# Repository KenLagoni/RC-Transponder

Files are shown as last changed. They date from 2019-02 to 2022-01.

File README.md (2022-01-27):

# RC Transponder (Locator Beacon)
After spending hours/days/weeks searching for lost RC Planes, I decided to design a single piece of hardware which can survive a crash and keep transmitting the GPS location.

## Design
<h4>The latest hardware version 12:</h4>

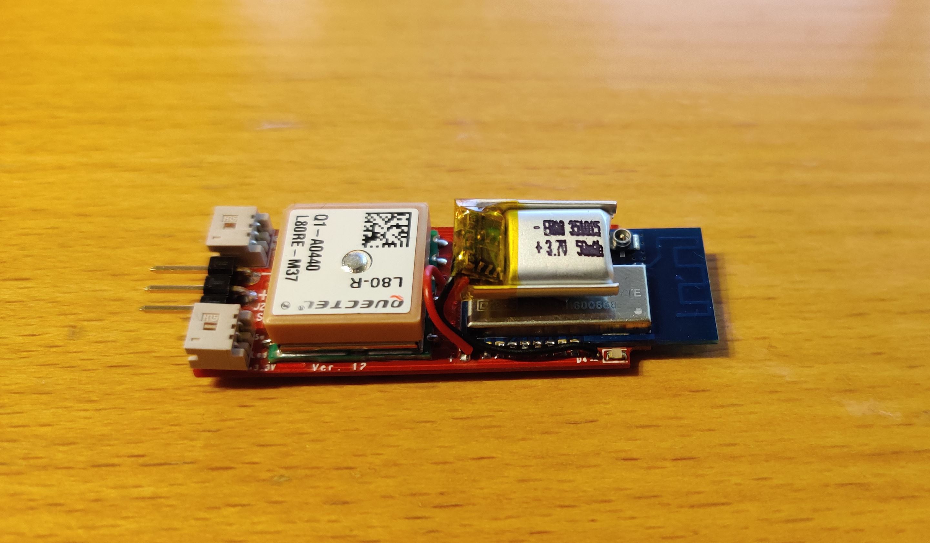
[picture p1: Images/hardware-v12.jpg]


### Features (Crashed mode)
1. Get GPS coordinates from on-board GPS sensor.
2. Keeps operating if power from plane is lost (like in a crash). 
3. Continue to operate after a crash for ~14h with a beacon transmitted every 10 second.
4. Recharge onboard battery from planes power supply. (50mAh Lipo cell)

### Features (Normal mode)
1. Operate as primary Frsky GPS sensor ID4 on SMART Port (using [pawelsky's](https://www.rcgroups.com/forums/showthread.php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) library).
2. Opperate as Mavlink to Passthrough converter for [Yaapu](https://github.com/yaapu/FrskyTelemetryScript) telemetry script for OpenTX.
3. Outputs other transponders location as StatusText messages via Passthrough to the Yaapu script. This means that when flying it can be used to listen for a crashed plane. This way other transponders will be displayed on the Radio:<br>*"ADSB([CALLSIGN]): [GPS_LATITUDE],[GPS_LONGITUDE],[NUMBEROFSAT],[FIX(2d/3d)],[HDOP]"*

### Features (Locator mode)
1. When placed in module bay of a radio running OpenTX, it will listen for other transponder beacons and send there coordinats to the Radio as seconday GPS sensor (ID5).

### Settings*
1. When connected via USB to a PC, it will show as Serial(COM) port and simple commands can be sent.
2. A unique callsign (up to 8 charactors) can be set via USB port (setcallsign [callsign]). 
<br>*(Settings are stored in NVM and only cleared when flashing new firmware).

### CPU (ATSAMD21 - ARM Cortex-M0+):
This project uses the SAMD21 MCU from the the Arduino MKRZero.

### Radio module (EBYTE E28-2G4M20S 100mW Lora):
In order to reduce size of the antenna, I tired the 2.4GHz modules from EBYTE.
I tested the EBYTE E28-2G4M20S (100mW) found that when using Lora modulation with SF7, BW= 400KHz and CR=4/5, I could get a range of ~2km between two modules.

### GPS Sensor (Sierra Wireless PA6H or Quectel-L80-R):
The PA6H from Global Tech (now Sierra Wireless) was the smallest GPS I could find with a decent chip antenna. (UBLOX CAM-M8 was not tested but could also be relevant).
The PA6H only transmit NMEA strings, so the CPU has some extra Work here.
On Hardware version 12 the GPS was changed to Quectel-L80-R due to availablilty. 

## Hardware Versions
1. Version 12 Latest HW, USB on side, 2xDF13_3PINS + 1xSIL3. (size: 46.6mmx18.6mm).
2. Version 11 10pin DF13 as input connector. (size: 43.5mmx18.0mm).
3. Version 10 (first prototype) now obsolete. (size: 44.0mmx20.0mm).
 
## Hardware Layout and manufacturing
Schematic and layout is done in Cadence/Allegro. This section is shown with now obsolete version 10 harwdare.
10 prototypes PCB was ordered with stencil and then it's "just" pick and place the components (I only made two).
Board after pick and place but before reflow (see [RocketScream for DIY reflow own](http://www.rocketscream.com/blog/product/tiny-reflow-controller/)).



After reflow:



Then the top side is soldered (GPS/Radio/battery/connector and one LED) (MicroSD Card for scale):


Finished unit with heat shrink (alongside the first 433MHz prototype):




## Range Testing
One transponder was mounted on a chair with a laptop on the field and the other was mounted in a plane.
The transponder in the plane was set to send every second and the PC on the ground logged all the data.



It worked very well, and there were no problem with the range.
To push the system to the limits, I then mounted the transponder from the plane in my car, and drove away. I found a point ~2km away which (almost line of sight) where the transponder still worked, but the RSSI was very low and some of the incomming packages had CRC errors:



## Low Power Test
When running firmware v2.00 on harware version 12, the opperating time was 14.5hours. (Beacon every 10sec. GPS update every 10mins).

## Low Temperature Test
TBD (Pending hardware version 12)

# Software
The Software reflects that I started out using Arduino MKRZERO and the Arduino program and then imported it to Atmel Studio.

## Radio driver (EBYTE E28-2G4M20S) (Semtech SX1280)
I was not able to find any Arduino libraries for the SX1280 chip, and thus I started out using the demo code from Semtech, which I had to make some changes to until I got something which worked.

## GPS NMEA decoder (GSP80Lite)
Was a library I once made for the Arduino ATMEGA328P, so i reused it and added some more features. It still only decode GPGGA strings, which means that Date, COG and speed is not read yet. (Used in the FrSky GPS sensor.)

## Frsky SPORT library
I used this great library from [pawelsky](https://www.rcgroups.com/forums/showthread.php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) However the ATSAMD21 chip is not supported and furthermore, I don't use single wire serial.
I did some changes to his library, including adding a passthoruth sensor for the Yaapu script. Please see the submodule [FrSky-S-Port-telemetry-library](https://github.com/KenLagoni/FrSky-S-Port-telemetry-library).

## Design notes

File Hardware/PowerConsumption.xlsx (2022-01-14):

Tested on HW: | 12
Interrupt interval | 1 | Hz
TX Interval | 0.2 | Hz
Battery Capacity | 50 | mAh
GPS ON sekunder | 60 | sek
GPS ON interval | 10 | min
 |  |  | Consumption [mA] |  | Time [ms] |  | Weighted |  | Energy [mAh]
 | SLEEP |  | 0.2 | mA | 990.6 | ms | 994.92 | ms | 0.1990
 | WAKE |  | 3 | mA | 4 | ms | 4 | ms | 0.0120
 | TX |  | 210 | mA | 27 | ms | 5.4 | ms | 1.1340
 | GPS ON |  | 2.50 | mA |  |  |  |  | 0.25
Total: |  |  |  |  |  |  |  |  | 1.59 | mAh
Total Time |  |  |  |  |  |  |  |  | 31.35 | Hours

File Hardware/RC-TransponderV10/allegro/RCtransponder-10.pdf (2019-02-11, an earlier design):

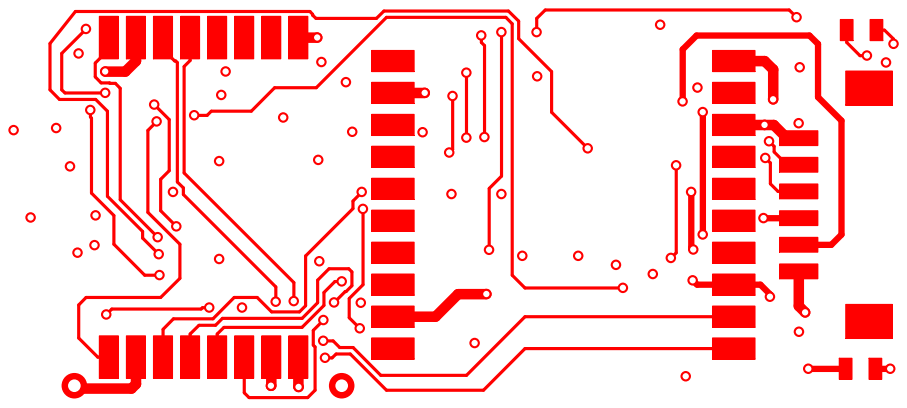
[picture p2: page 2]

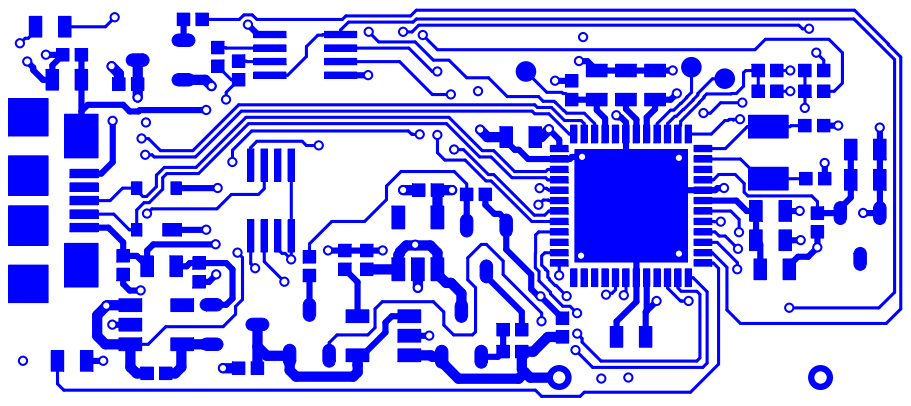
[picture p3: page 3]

FIGURE | FINISHED_SIZE | TOLERANCE_DRILL | PLATED | QTY
| 0.3 | +0.05/-0.05 | PLATED | 96
| 0.6 | +0.08/-0.08 | PLATED | 2
| 3.0 | +0.1/-0.1 | PLATED | 1

ALL UNITS ARE IN MILLIMETERS

DRILL CHART: TOP to BOTTOM

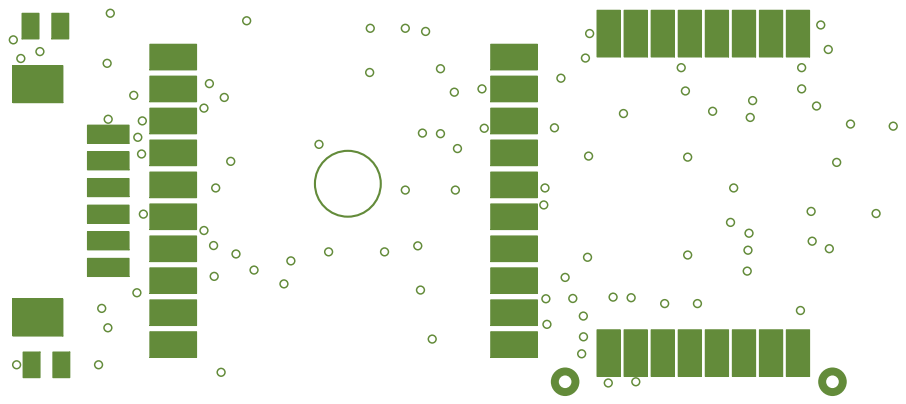
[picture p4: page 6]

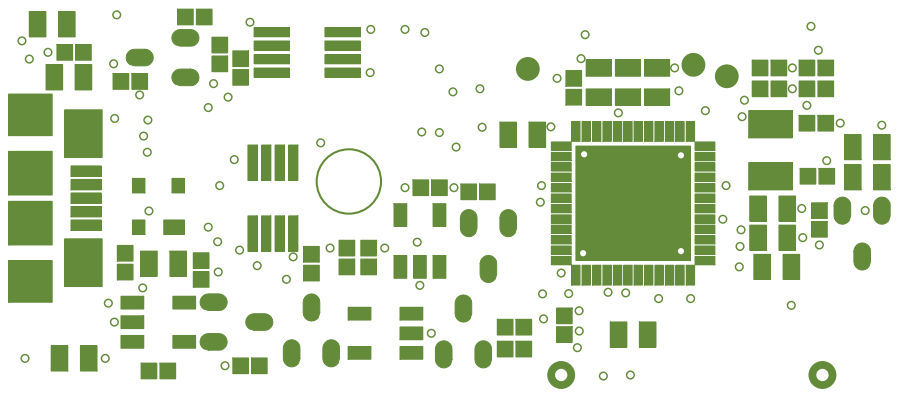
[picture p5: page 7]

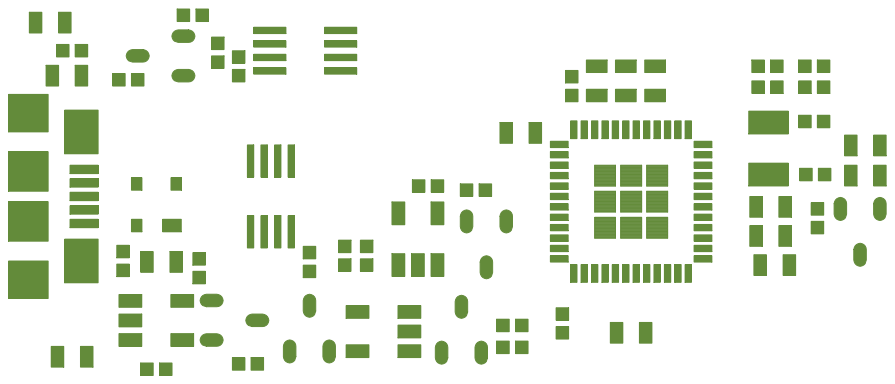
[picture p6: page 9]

D4

J1

D7

J4 | J2

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
C15FB2

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
C6 U3

Q1

Q2

C4 R7

RESET

R2
+

R4 C3

C10

C9

U4

R16

C18

C11
C17

SWCLK

C12

C13

FB1

Y1

R9

R10

SWDIO

R6 D3

C5

C2

R8

R11

C7

C8

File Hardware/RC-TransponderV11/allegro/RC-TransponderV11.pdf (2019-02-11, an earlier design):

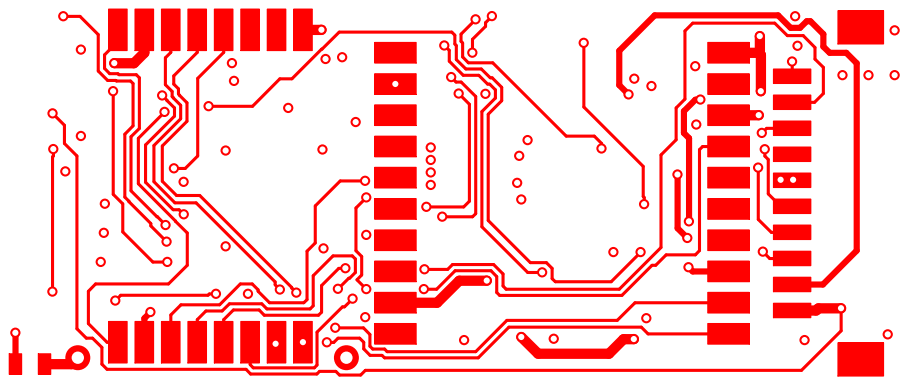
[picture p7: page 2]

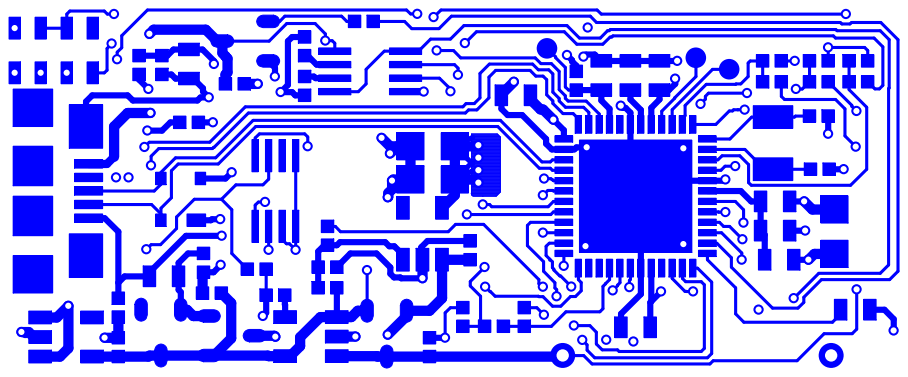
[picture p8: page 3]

FIGURE | FINISHED_SIZE | TOLERANCE_DRILL | PLATED | QTY
| 0.3 | +0.05/-0.05 | PLATED | 112
| 0.6 | +0.08/-0.08 | PLATED | 2
| 3.0 | +0.1/-0.1 | PLATED | 1

ALL UNITS ARE IN MILLIMETERS

DRILL CHART: TOP to BOTTOM

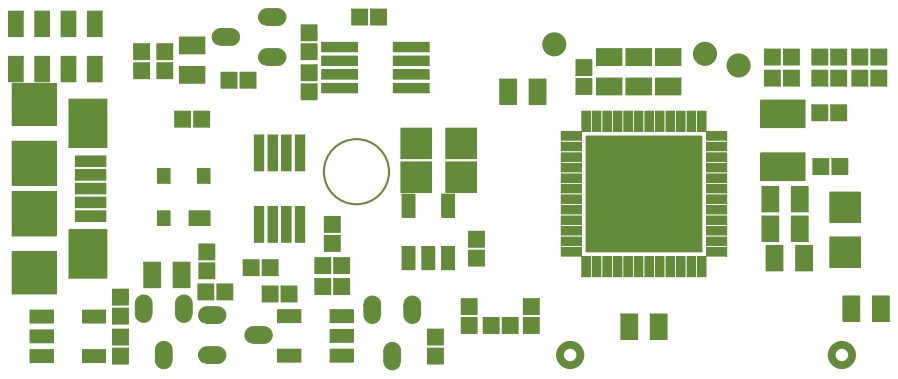
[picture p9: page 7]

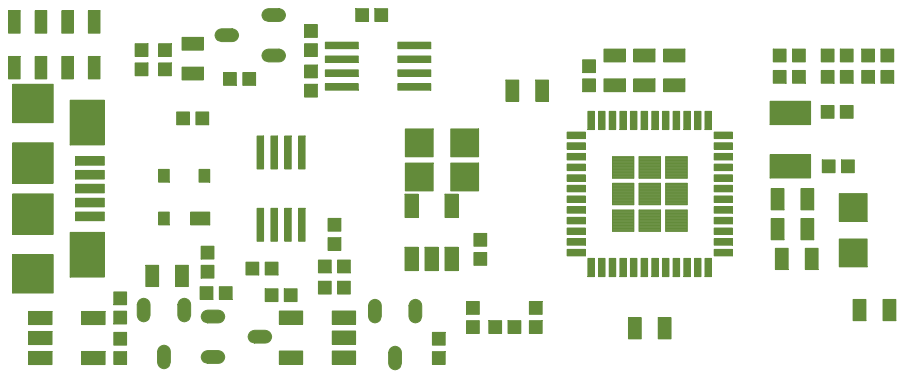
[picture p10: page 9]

J1U10 U1

D4

U2

U9

C1 C16

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
R18 R19

Q4

U3

C22

U7

R15

C3

R29 R27

C6

C4

+

C20

C10

RESET

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
- R13

C23

C5

C2

R8

R11
R30

R31

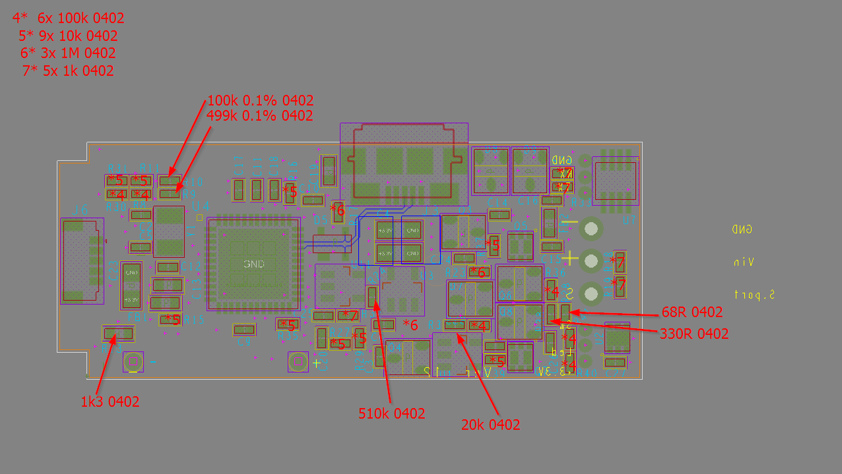
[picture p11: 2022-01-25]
Hardware/RC-TransponderV12/allegro/pickandplace_resistors.png

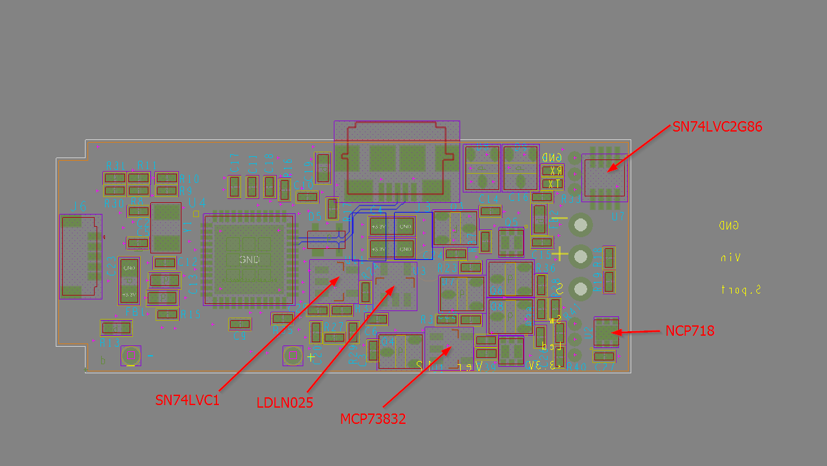
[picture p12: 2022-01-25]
Hardware/RC-TransponderV12/allegro/pickandplace_IC.png

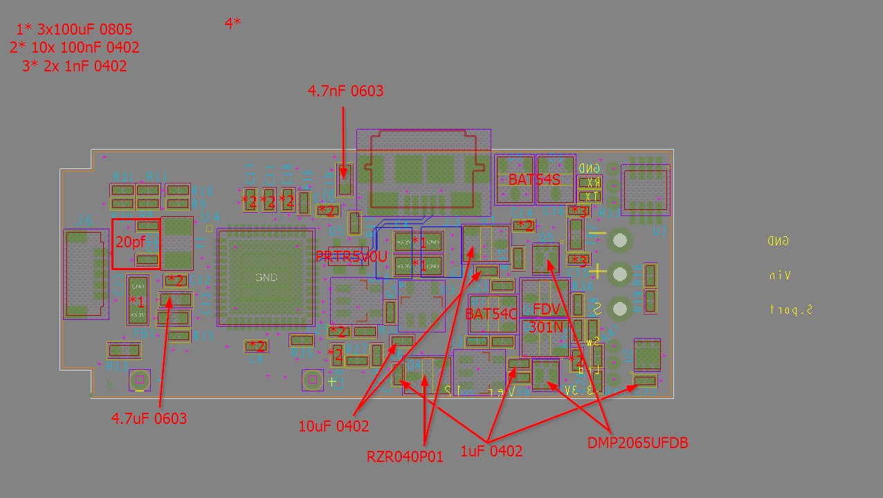
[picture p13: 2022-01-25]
Hardware/RC-TransponderV12/allegro/pickandplace_capacitors.png

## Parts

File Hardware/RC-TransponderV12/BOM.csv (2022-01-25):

History Revised: Friday, January 07, 2022
RC Transponder 2.4 GHz Revision: 12
Bill Of Materials January 7,2022 | Page1
Item | Quantity | Reference | Part | PCB | Manufacturer | Manufacturer PN | Farnell Part Number | Farnell Price
______________________________________________
1 | 1 | + | Vbat+ | testpin-0_6mm
2 | 1 | - | Vbat- | testpin-0_6mm
3 | 3 | C1,C3,C27 | 1uF/10V | r_0402 | Generic | 1uF, 0402, 10V | 2320776 | 0.0519
4 | 2 | C2,C5 | 20pF | r_0402 | Generic | 20pF, 0402, 50V, 5% | 1740573 | 0.197
5 | 3 | C4,C22,C23 | 100uF/4V | r_0805 | Generic | 100uF, 0805, 4V, 20% | 2611937 | 5.43
6 | 1 | C6 | 10uF/6V3 | r_0402 | Generic | 10uF, 0402, 6V3, 20% | 2218854 | 2.01
7 | 10 | C9,C10,C11,C12,C14,C17,C18,C20,C25,C26 | 100nF | r_0402 | Generic | 100nF, 0402, 16V 20% | 2524679 | 0.0709
8 | 1 | C13 | 4.7uF | r_0603 | Generic | GRT188C81E475KE13D | 2672151 | 1.68
9 | 2 | C15,C16 | 1nF | r_0402 | Generic | 1nF, 0402, 25V, 10% | 2332485 | 0.197
10 | 1 | C19 | 4.7nF / 100V | r_0603 | Walsin | 0603B472K101CT | 2495361 | 0.34
11 | 1 | C24 | 10uF/6V3 | r_0402 | Generic | 10uF, 0402, 6V3 | 2218854 | 2.01
12 | 1 | D4 | LSQ976-Z | r_0603 | OSRAM | LSQ976-Z | 1226390 | 0.8813
13 | 1 | D5 | PRTR5V0U2X | r_sot143B | NXP | PRTR5V0U2X,215 | 1524157 | 1.66
14 | 1 | D7 | BAT54C | r_sot23_123 | On Semi | BAT54CLT1G | 1431112 | 0.8448
15 | 2 | D8,D9 | BAT54S | r_sot23 | NXP | BAT54S | 1081194 | 0.47
16 | 2 | FB1,FB2 | 470R@100MHz | r_0603 | Murata | BLM18PG471SN1D | 1515745 | 0.2592
17 | 1 | J2 | 3x2.54mm | l_conn_1x3way-2_54mm_angled | Würth | 61300311021 | 2356177 | 1.46
18 | 1 | J3 | ZX62-AB-5PA(31) | r_usb-zx62-ab-5pa_31_ | Hirose | ZX62-AB-5PA(31) | 2663341 | 4.06
19 | 2 | J4,J5 | 3x1_1.25mm DF13 connector | l_conn_DF13-3P-1_25DS | Hirose | DF13-3P-1.25DS(20) |  | 2.66
20 | 1 | J6 | 5x1_DF52_0.8mm connector | r_conn_DF52-5S-0_8H | Hirose | DF52-5S-0.8H(21) | 2853823 | 2.27
21 | 1 | PCB1 | TransponderRC2_4-12 |  | jlcpcb.com | Transponder V12 |  | 35.87
22 | 1 | P1 | Heat Shrink 6cm |  | PRO POWER | PP001992 | 2852319 | 6.12
23 | 2 | Q3,Q4 | RZR040P01 | r_sot23 | ROHM | RZR040P01TL | 2143957 | 3.6192
24 | 2 | Q5,Q7 | DMP2065UFDB | r_u-dfn2020-6 | Diodes Inc. | DMP2065UFDB-7 | 2709536 | 1.536
25 | 1 | Q5 | DMP2065UFDB | r_u-dfn2020-6 | Diodes Inc. | DMP2065UFDB-7 | 2709536 | 1.54
26 | 2 | Q6,Q8 | FDV301N | r_sot23 | On Semi | FDV301N | 9845011 | 1.48
27 | 1 | R3 | 20k | r_0402 | Generic | 20k,1%,0402 | 2130457 | 0.08
28 | 6 | R8,R22,R30,R36,R40,R41 | 100k | r_0402 | Generic | 100k,1%,0402 | 2130514 | 0.08
29 | 1 | R9 | 499k 0.1% | r_0402 | NEOHM - TE CONNECTIVITY | CPF0402B499KE1 | 3579089 | 1.46
30 | 1 | R10 | 100k 0.1% | r_0402 | Generic | 100k, 0402, 50V, 0.1% | 2838458 | 1.79
31 | 9 | R11,R15,R16,R27,R29,R31,R35,R37,R39 | 10k | r_0402 | Generic | 10k,1%,0402 | 2130433 | 0.1
32 | 1 | R13 | 1k3 | r_0603 | Generic | 1k3,1%,0603 | 2447277 | 0.1
33 | 3 | R17,R23,R42 | 1M | r_0402 | Generic | 1M,1%,0402 | 2447127 | 0.08
34 | 5 | R18,R19,R32,R33,R34 | 1k | r_0402 | Generic | 1k,1%,0402 | 2331474 | 0.1
35 | 1 | R24 | 510k | r_0402 | Generic | 510k,1%,0402 | 1458807 | 0.08
36 | 1 | R28 | 68R | r_0402 | Generic | 68R,1%,0402 | 2379929 | 0.1
37 | 1 | R38 | 330R | r_0402 | Generic | 330R,1%,0402 | 2861394 | 0.08
38 | 1 | U1 | MCP73831T-2ACI | r_sot23-5pin | Microchip | MCP73831T-2ACI/OT | 1332158 | 4.8
39 | 1 | U2 | NCP718BMT500TBG | r_wdfn-6 | On Semi | NCP718BMT500TBG | 3010497 | 2.02
40 | 1 | U3 | LDLN025M33R | r_sot23-5pin | ST | LDLN025M33R | 2851941 | 5
41 | 1 | U4 | ATSAMD21G18A-48 | r_qfn48_7x7mm | Microchip | ATSAMD21E18A-MUT | 2920752 | 17.76
42 | 1 | U7 | SN74LVC2G86DCTR | r_PDSO-G8 | Texas Instruments | SN74LVC2G86DCTR | 2334919 | 3.28
43 | 1 | U8 | E28-2G4M20S | r_rfE28-2g4m20s | Ebyte | e28-2g4m20s |  | 64
44 | 1 | U10 | Quectel-L80-R | r_L80_GPS | Quectel | L80-R |  | 30
45 | 1 | U11 | SN74LVC1G79 | r_sot23-5pin | Texas Instruments | SN74LVC1G79DBVR | 2342442 | 1.84
46 | 1 | Vbat1 | Li-ion 3.7V 50mAh |  | Ebay / Aliexpress | Li-ion Cell 50mAh Size: 351015 |  | 15
47 | 1 | Y1 | 32.768kHz | r_xtal-abs07 | Abracon | ABS07-32.768KHZ-T | 2101347 | 3.0336

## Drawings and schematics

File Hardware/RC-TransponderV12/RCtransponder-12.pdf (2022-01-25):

D | D
C | C
B | B
A | A
Revision | History | Responsible
1.00 | 1 st revision (Now obsolete) | Kenneth Lagoni Olsen

# REVISION 1.20

# RC Transponder 2.4GHz

1.10

DIO1 connection added to CPU.
R8 must be changed to ensure Vin-pin doesn't exceed 3.3V when input is 11V. Pull-down on serial input (to avoid junk trigger if floating).

## Kenneth Lagoni Olsen

1.20

## Updated:

Input regulator U2 changed to be able to handle input voltage up to 24V (before 11V was max). Input power selectors changed from Diode to Fet type, to ensure minimal voltage drop when on. Regulator U3 changed to LDLN025M33R.
Input connector changed from 1x10 DF13 to 2x3 DF13 and 1 SIL3 for more rubust connectors to RX. Vbat resistors R9 / R10 changed and upgraded to 0.1% for better accuracy.
5V measuring resistor R30 changed to 100K. And also changed to Vusb.
GPS changed from PA6H to Quectel LR80. Also now with Reset option from MCU.
Li-ion charger U1 changed to MCP73831T-2ACI for better Charge state output.

## Removed:

Pressure sensor U9 removed.
RC / SBUS input removed.

## Added:

Power On from MCU is now via flip-flop U11 in order to allow software to reboot without losing power. Charge state input to MCU for better battery monitoring.
J6 connector for easy bootloader programming.

## Kenneth Lagoni Olsen

Title

Size | Document Number | Rev
Date: | Sheet | of
RC Transponder 2.4 GHz | 12

History

A3

Friday, January 07, 2022 | 1 | 3
RC Transponder 2.4 GHz | 12

History

Friday, January 07, 2022 | 1 | 3
RC Transponder 2.4 GHz | 12

History

Friday, January 07, 2022 | 1 | 3

# Input Connectors

# FrSky Smart Port

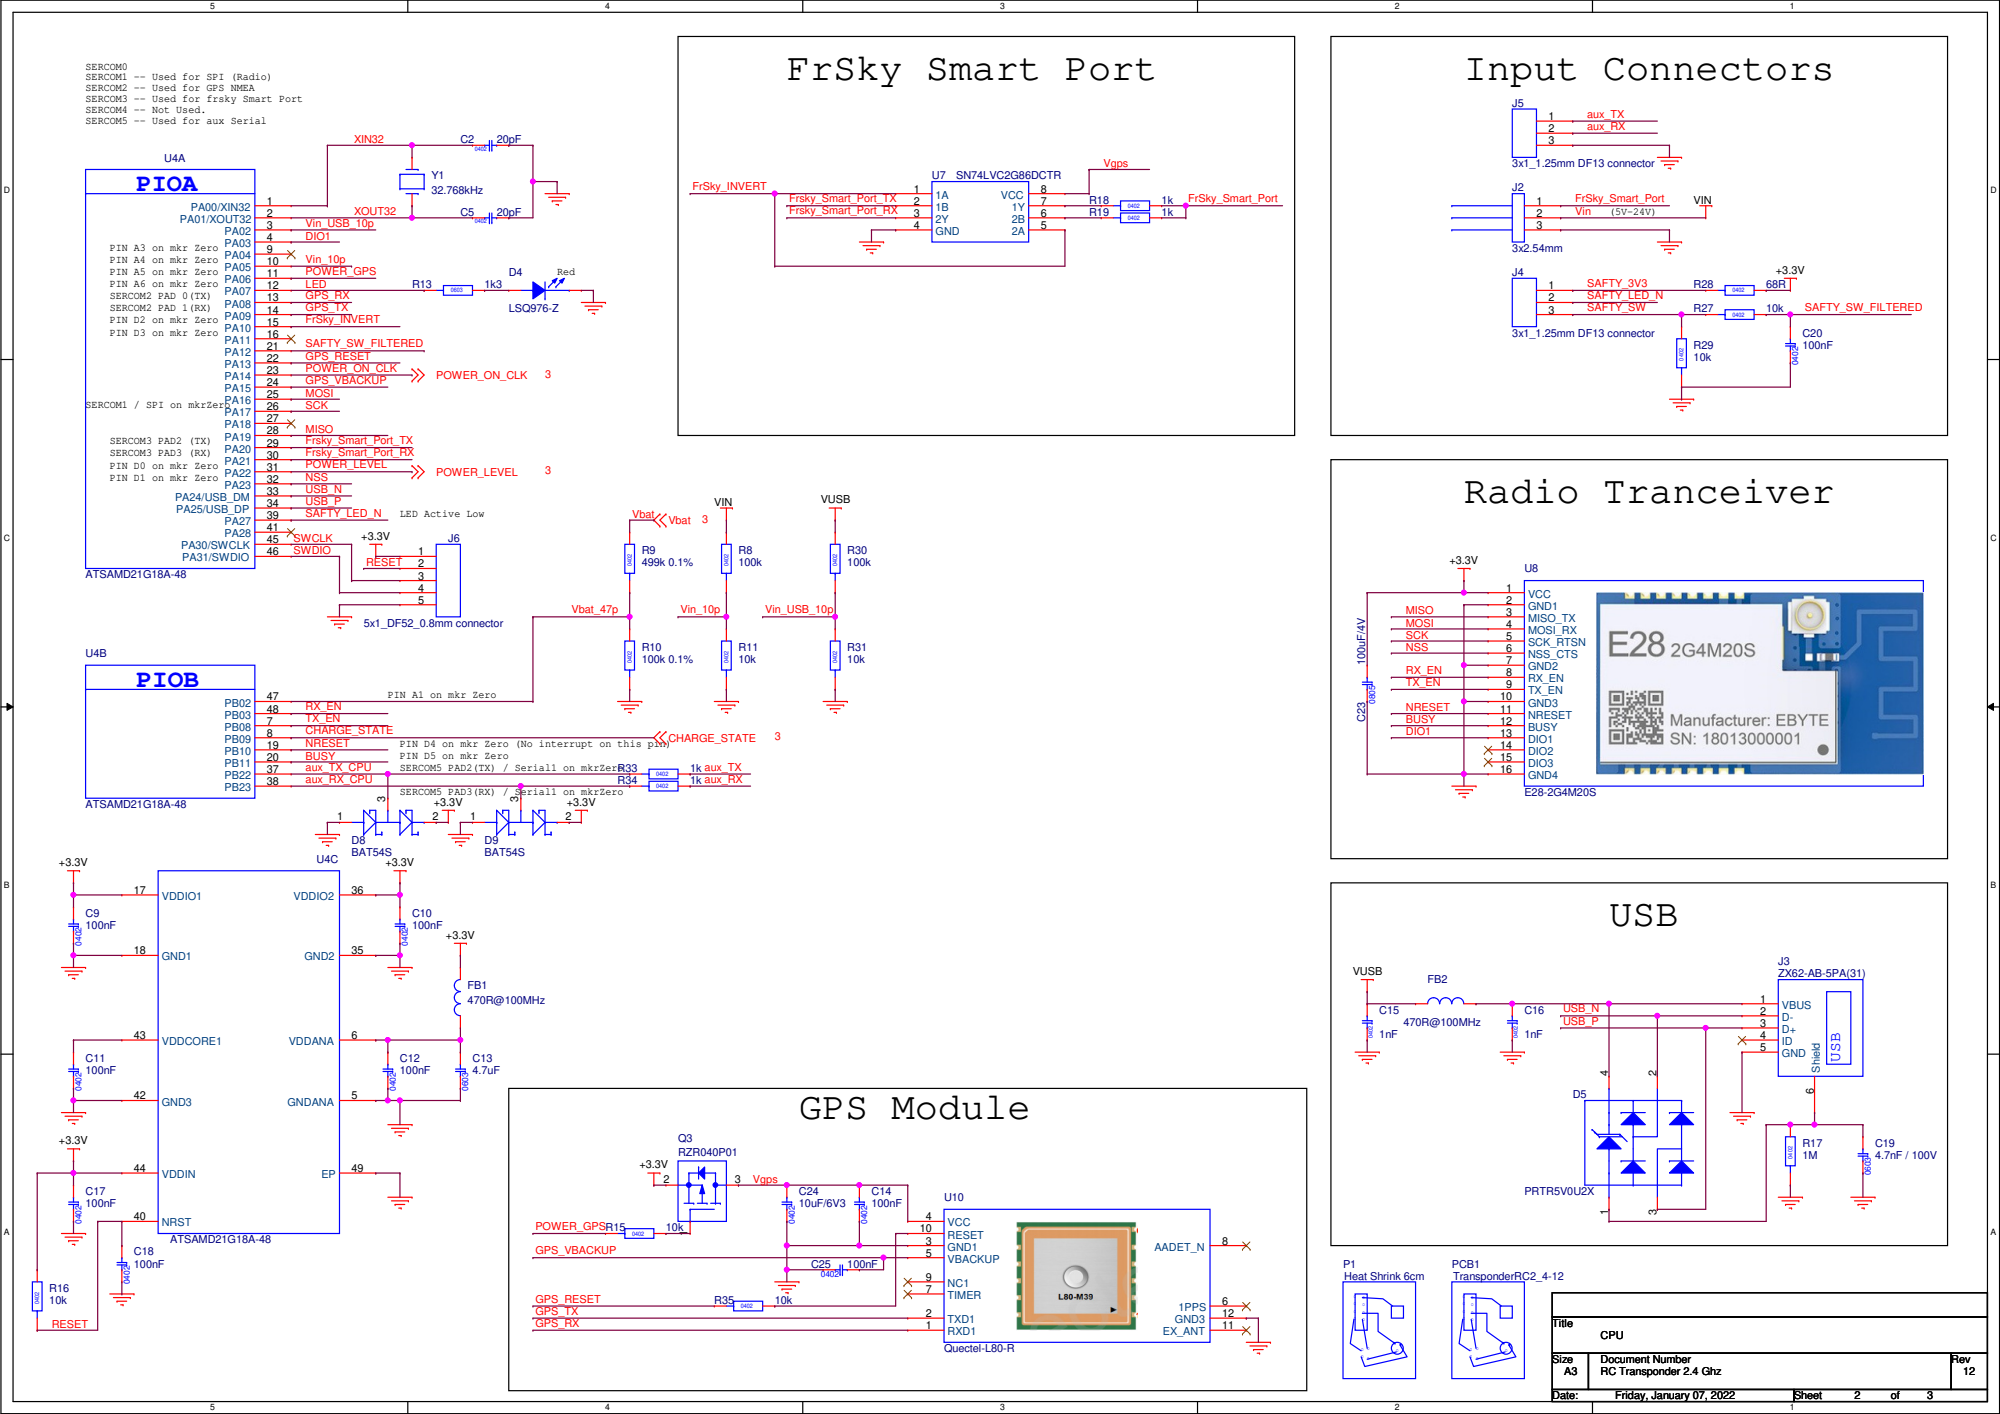
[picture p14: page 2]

SERCOM0
SERCOM1 -- Used for SPI (Radio)
SERCOM2 -- Used for GPS NMEA
SERCOM3 -- Used for frsky Smart Port
SERCOM4 -- Not Used.
SERCOM5 -- Used for aux Serial

PIN A3 on mkr Zero
PIN A4 on mkr Zero
PIN A5 on mkr Zero
PIN A6 on mkr Zero
SERCOM2 PAD 0(TX)
SERCOM2 PAD 1(RX)
PIN D2 on mkr Zero
PIN D3 on mkr Zero

SERCOM3 PAD2 (TX)
SERCOM3 PAD3 (RX)
PIN D0 on mkr Zero
PIN D1 on mkr Zero

PIN A1 on mkr Zero

PIN D4 on mkr Zero (No interrupt on this pin)
PIN D5 on mkr Zero
SERCOM5 PAD2(TX) / Serial1 on mkrZero

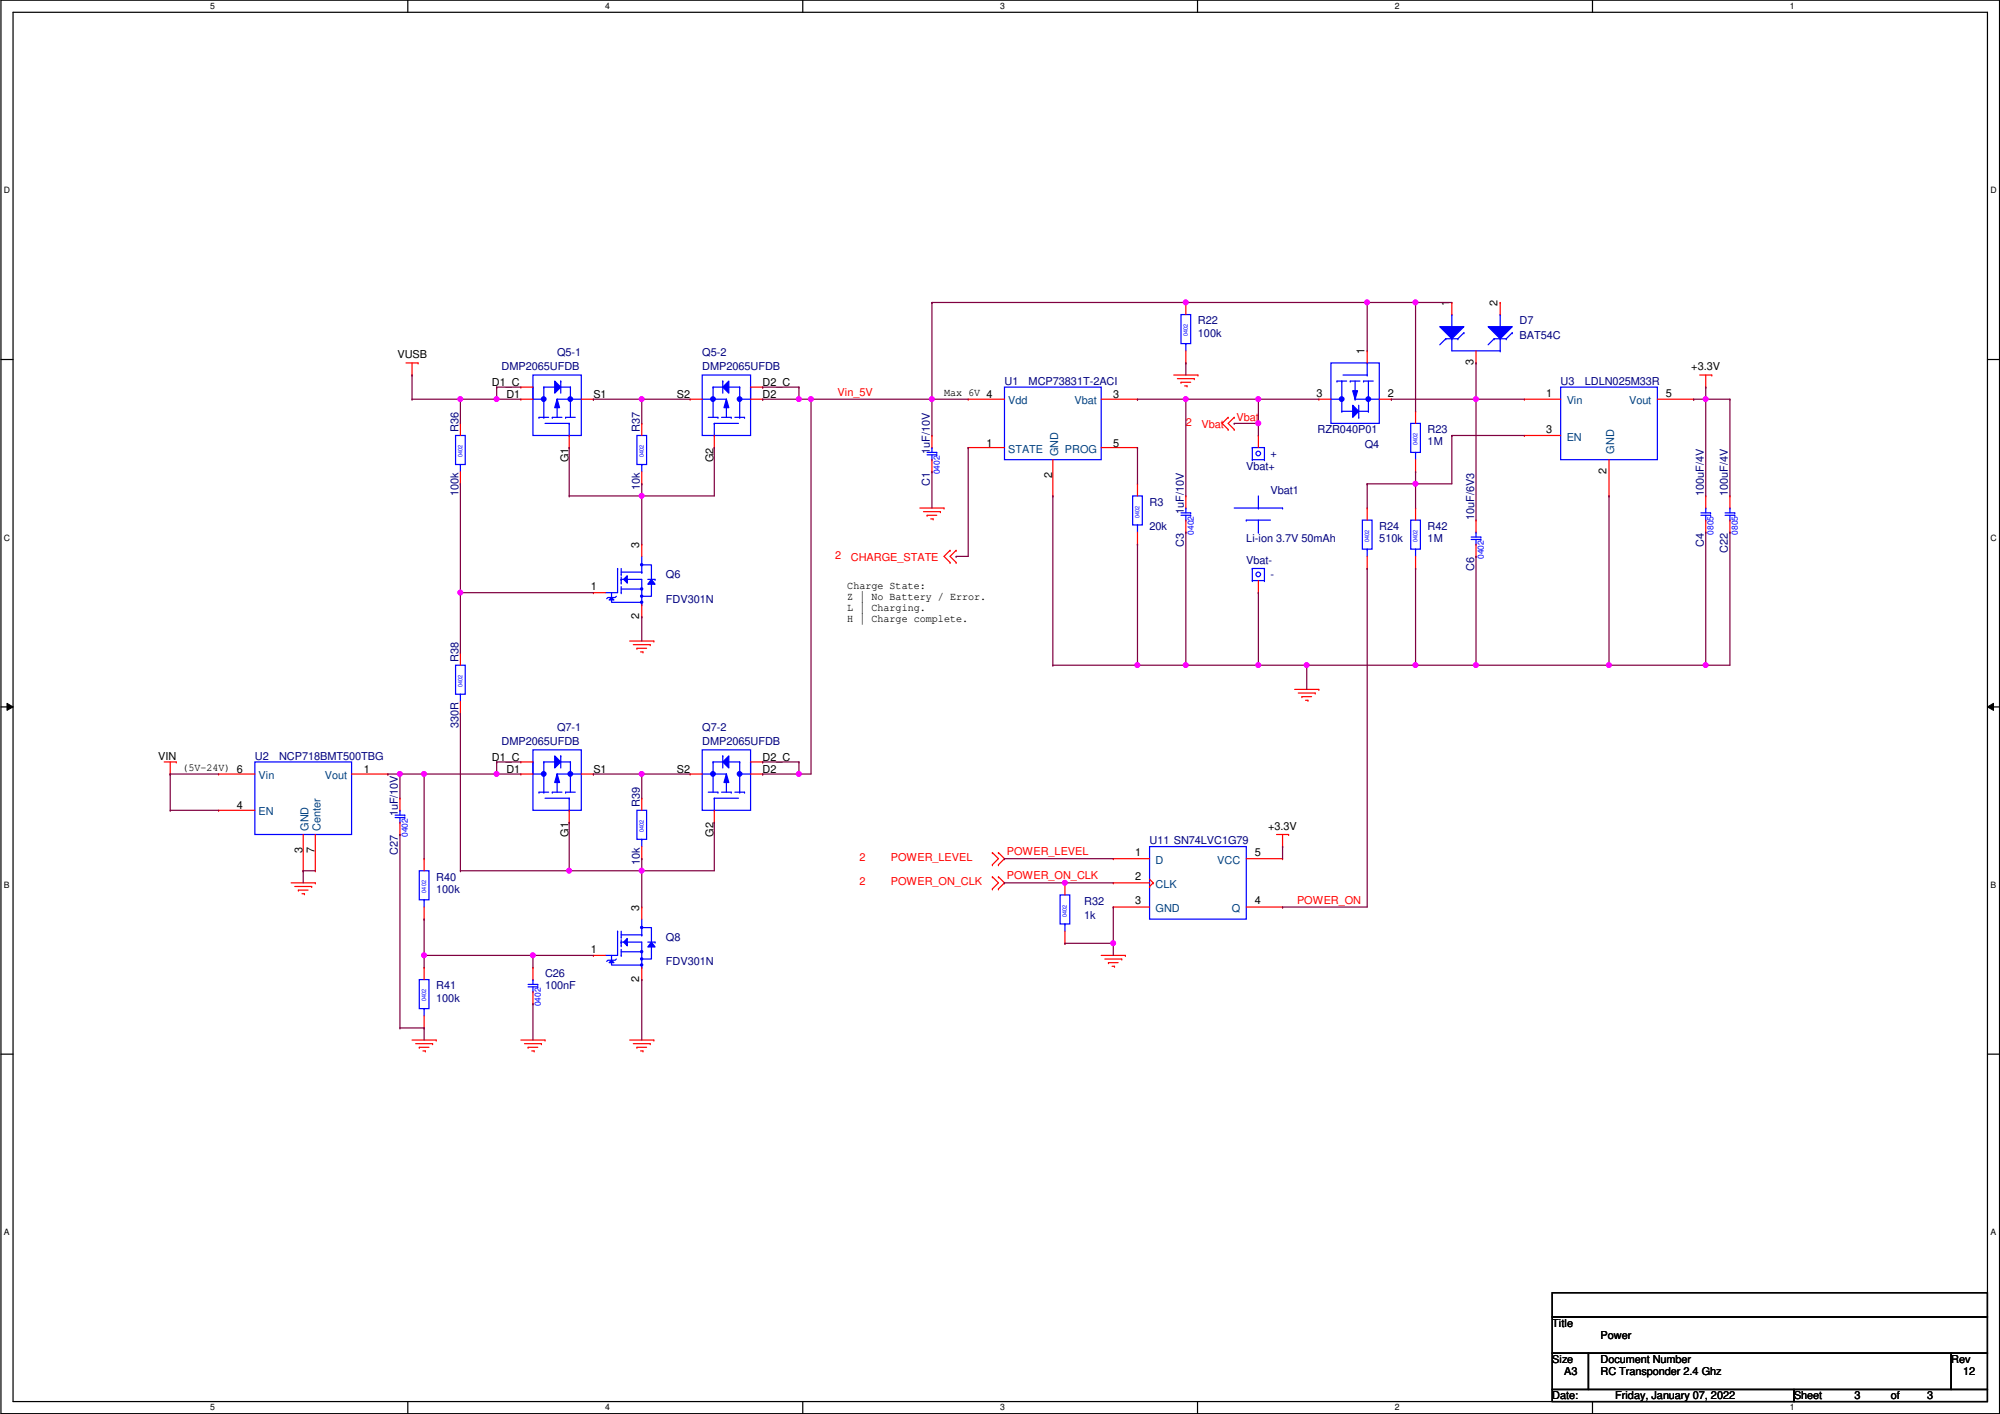
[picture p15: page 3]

Charge State: Z | No Battery / Error. L | Charging. H | Charge complete.

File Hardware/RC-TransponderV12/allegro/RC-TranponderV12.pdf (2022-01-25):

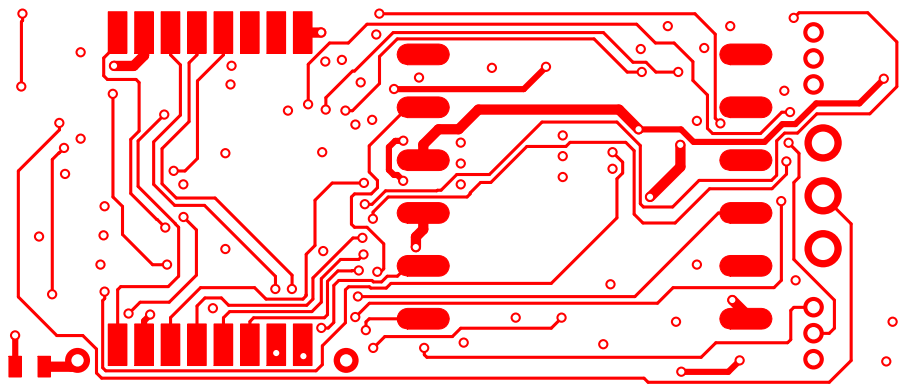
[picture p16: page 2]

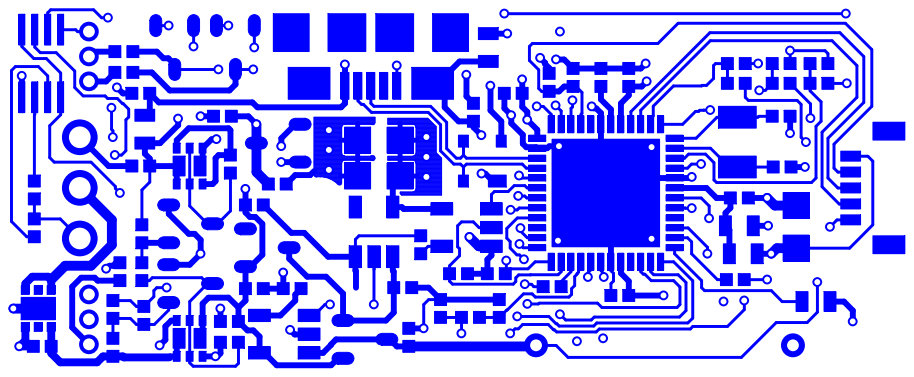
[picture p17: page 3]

FIGURE | FINISHED_SIZE | TOLERANCE_DRILL | PLATED | QTY
| 0.3 | +0.05/-0.05 | PLATED | 106
| 0.6 | +0.003/-0.003 | PLATED | 6
| 0.6 | +0.08/-0.08 | PLATED | 2
| 1.1 | +0.05/-0.05 | PLATED | 3

ALL UNITS ARE IN MILLIMETERS

DRILL CHART: TOP to BOTTOM

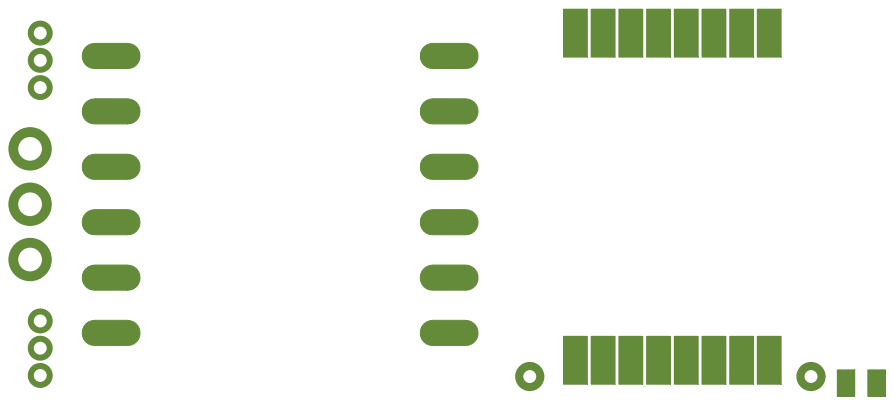
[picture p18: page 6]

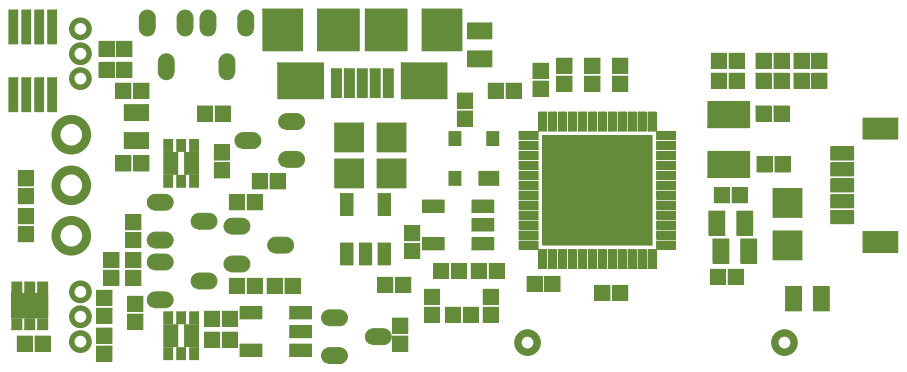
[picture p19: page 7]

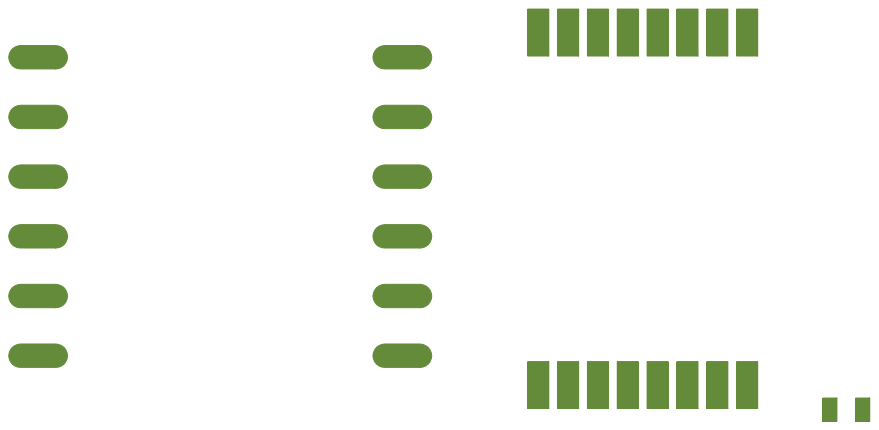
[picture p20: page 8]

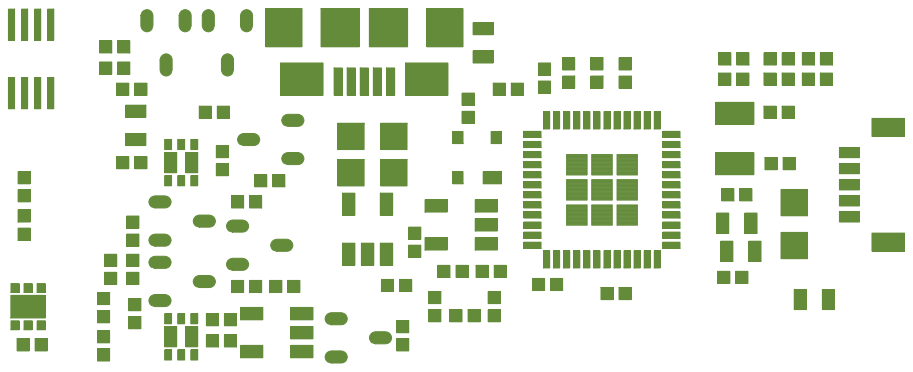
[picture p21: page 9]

J4

J2

J5

U12 | U8

D4

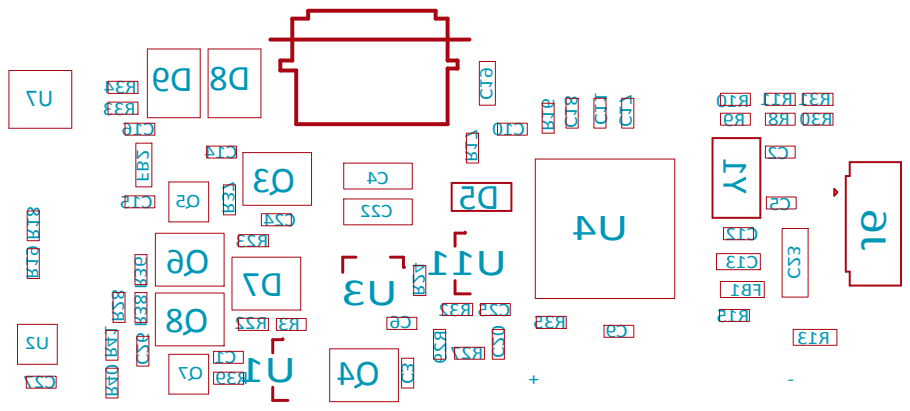
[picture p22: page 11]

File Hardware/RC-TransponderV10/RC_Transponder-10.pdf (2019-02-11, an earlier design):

# REVISION 1.00

# RC Transponder 2.4GHz

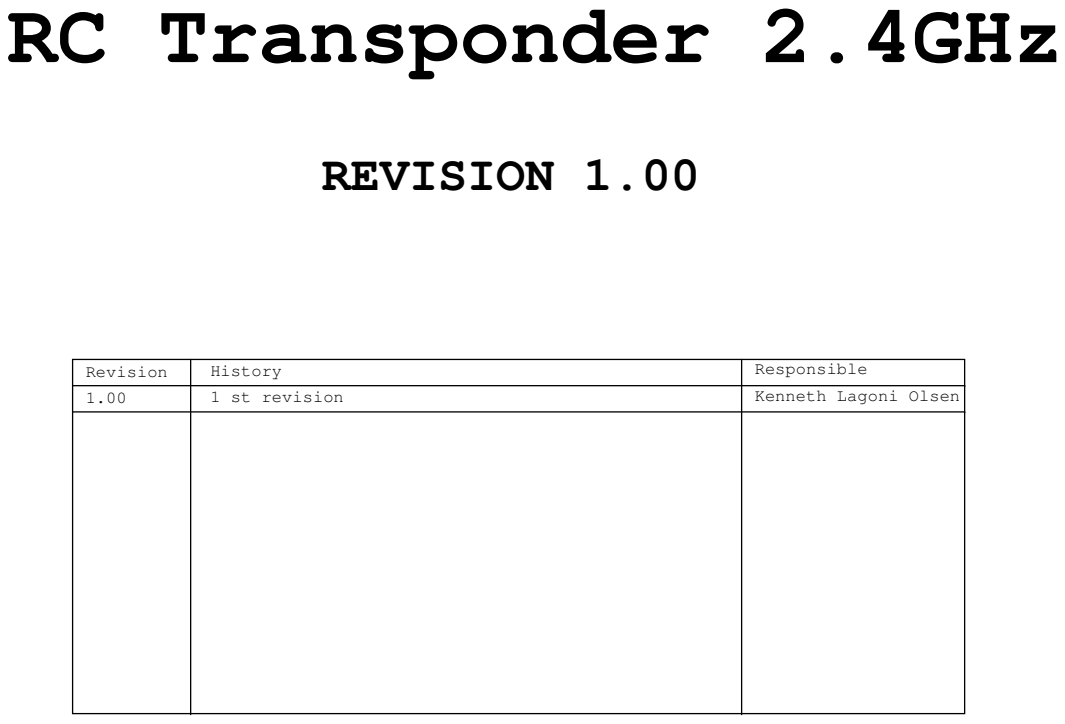
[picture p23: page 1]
Revision; History; Responsible; 1 st revision; Kenneth Lagoni Olsen; Title; Size; Document Number; Rev; Date:; Sheet; RC Transponder 2.4 Ghz; Tuesday, December 18, 2018

# PIOA

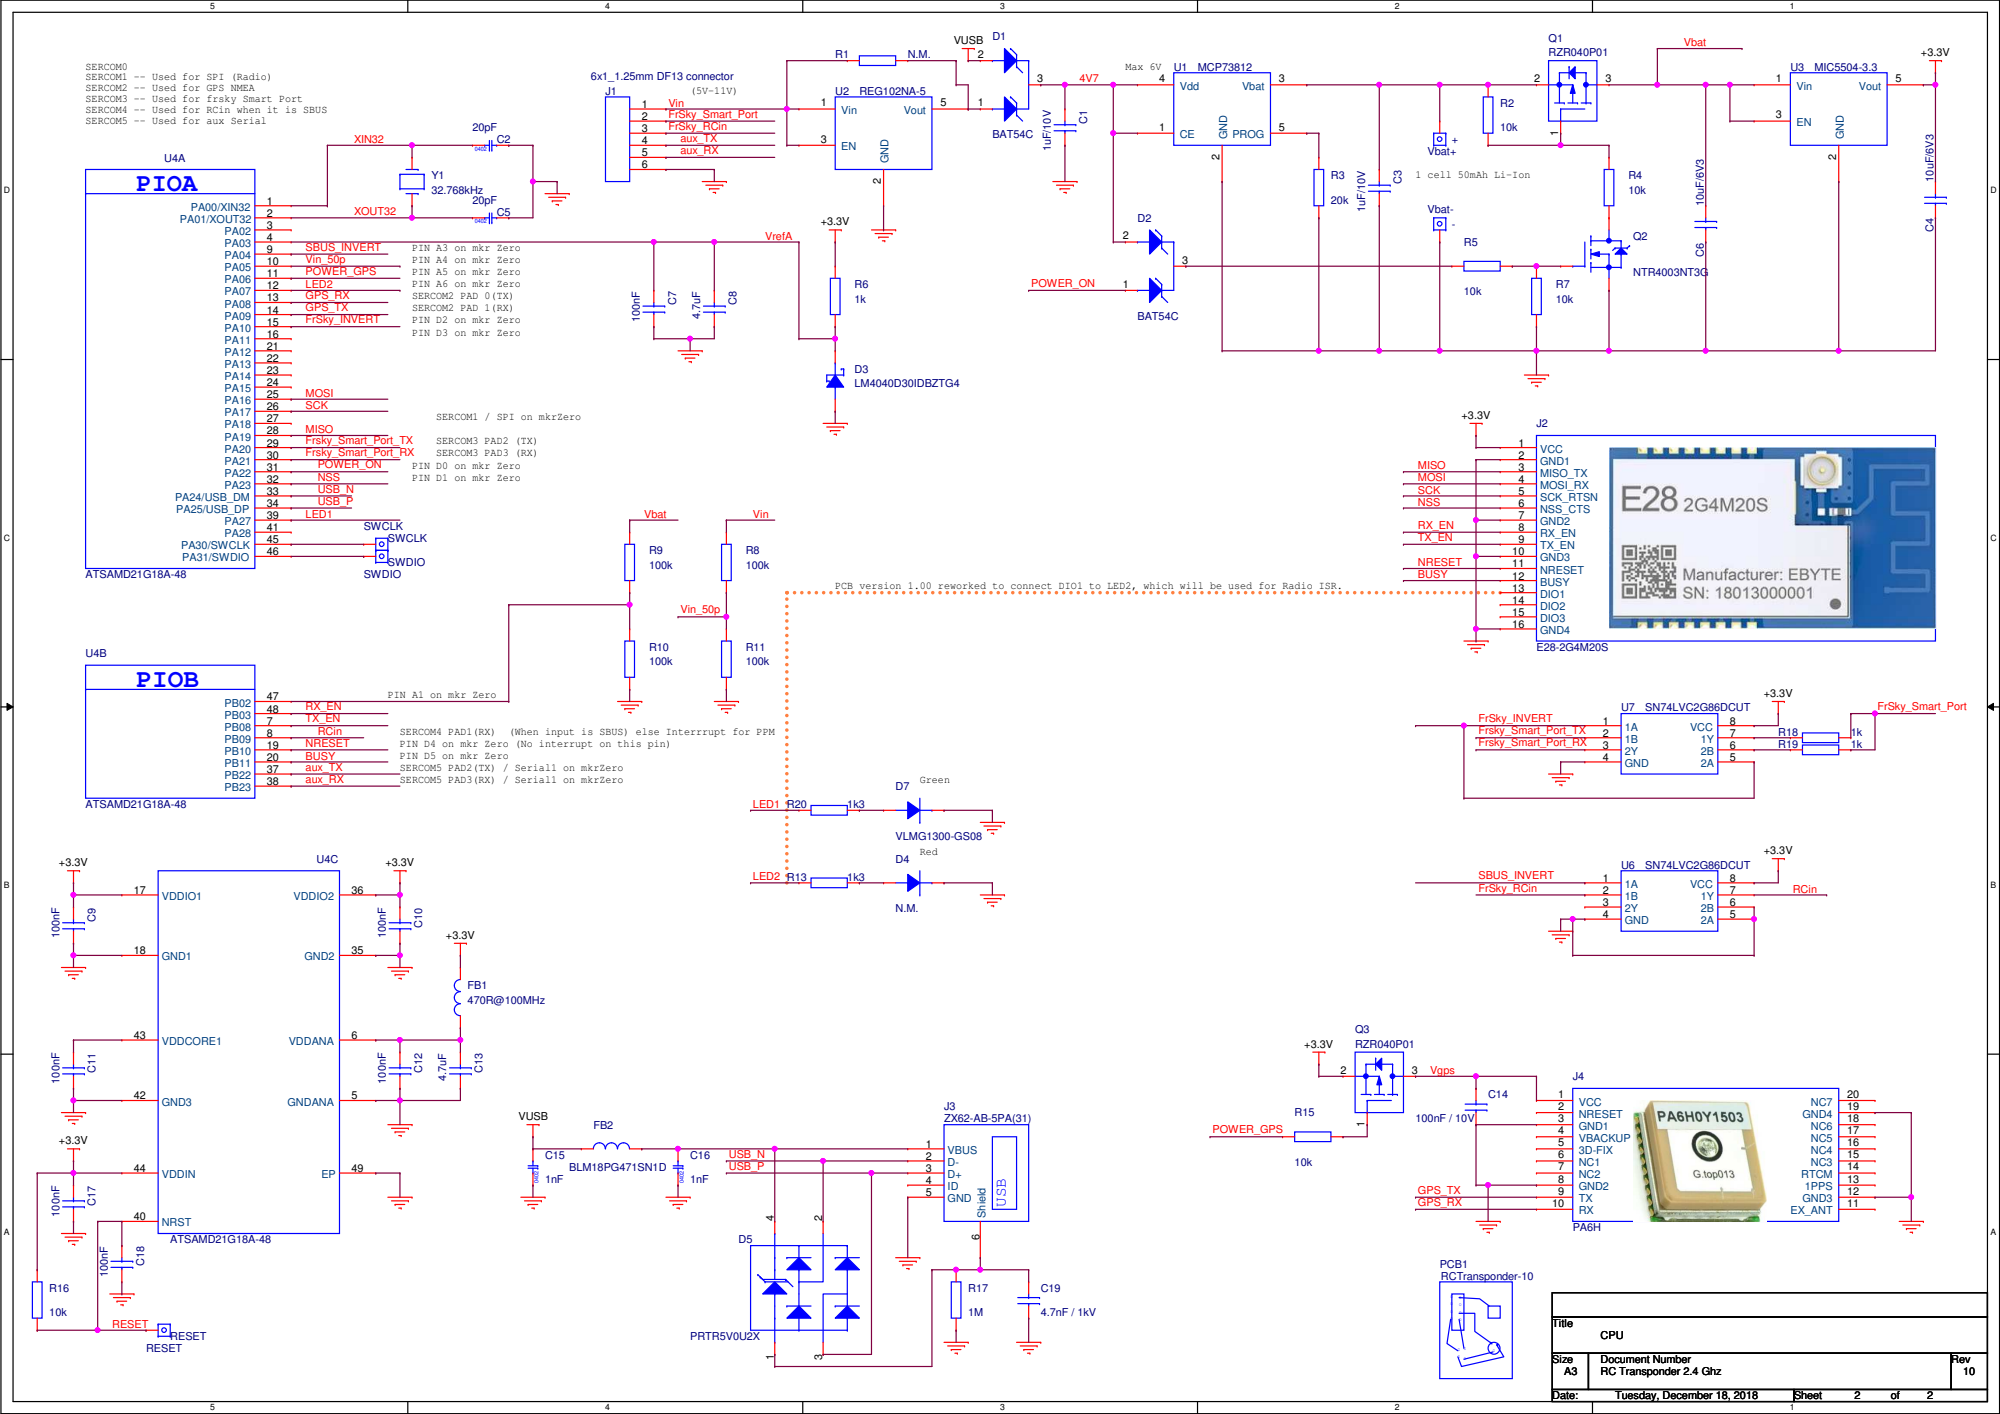
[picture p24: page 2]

VUSB | Q1 | Vbat

SERCOM0
SERCOM1 -- Used for SPI (Radio)
SERCOM2 -- Used for GPS NMEA
SERCOM3 -- Used for frsky Smart Port
SERCOM4 -- Used for RCin when it is SBUS
SERCOM5 -- Used for aux Serial

PIN A3 on mkr Zero
PIN A4 on mkr Zero
PIN A5 on mkr Zero
PIN A6 on mkr Zero
SERCOM2 PAD 0(TX)
SERCOM2 PAD 1(RX)
PIN D2 on mkr Zero
PIN D3 on mkr Zero

SERCOM3 PAD2 (TX)
SERCOM3 PAD3 (RX)
PIN D0 on mkr Zero
PIN D1 on mkr Zero

PCB version 1.00 reworked to connect DIO1 to LED2, which will be used for Radio ISR.

PIN A1 on mkr Zero

PIN D4 on mkr Zero (No interrupt on this pin)
PIN D5 on mkr Zero
SERCOM5 PAD2(TX) / Serial1 on mkrZero
SERCOM5 PAD3(RX) / Serial1 on mkrZero

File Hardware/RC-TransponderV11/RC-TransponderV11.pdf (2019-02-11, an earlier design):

# REVISION 1.10

# RC Transponder

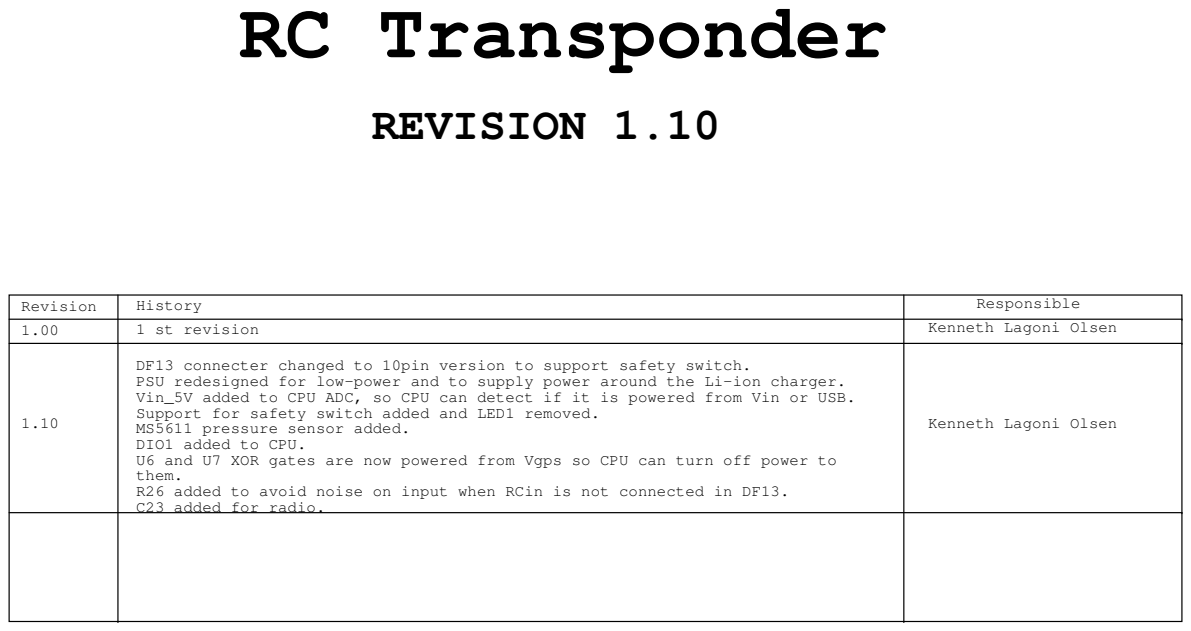
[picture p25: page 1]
Revision; History; Responsible; 1 st revision; Kenneth Lagoni Olsen; Title; Size; Document Number; Rev; Date:; Sheet; RC-Transponder; Monday, February 11, 2019

DF13 connecter changed to 10pin version to support safety switch.
PSU redesigned for low-power and to supply power around the Li-ion charger.
Vin_5V added to CPU ADC, so CPU can detect if it is powered from Vin or USB.
Support for safety switch added and LED1 removed.
MS5611 pressure sensor added.
DIO1 added to CPU.
U6 and U7 XOR gates are now powered from Vgps so CPU can turn off power to
them.
R26 added to avoid noise on input when RCin is not connected in DF13.
C23 added for radio.

Kenneth Lagoni Olsen

# PIOA


VUSB

SERCOM0
SERCOM1 -- Used for SPI (Radio)
SERCOM2 -- Used for GPS NMEA
SERCOM3 -- Used for frsky Smart Port
SERCOM4 -- Used for RCin when it is SBUS
SERCOM5 -- Used for aux Serial

PIN A3 on mkr Zero
PIN A4 on mkr Zero
PIN A5 on mkr Zero
PIN A6 on mkr Zero
SERCOM2 PAD 0(TX)
SERCOM2 PAD 1(RX)
PIN D2 on mkr Zero
PIN D3 on mkr Zero

SERCOM3 PAD2 (TX)
SERCOM3 PAD3 (RX)
PIN D0 on mkr Zero
PIN D1 on mkr Zero

PIN A1 on mkr Zero

PIN D4 on mkr Zero (No interrupt on this pin)
PIN D5 on mkr Zero
SERCOM5 PAD2(TX) / Serial1 on mkrZero
SERCOM5 PAD3(RX) / Serial1 on mkrZero

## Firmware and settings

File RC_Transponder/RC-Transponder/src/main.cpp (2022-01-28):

/*
RC Transponder

Copyright (c) 2019 Lagoni
Not for commercial use

THE SOFTWARE IS PROVIDED "AS IS", WITHOUT WARRANTY OF ANY KIND, EXPRESS OR IMPLIED, INCLUDING 
BUT NOT LIMITED TO THE WARRANTIES OF MERCHANTABILITY, FITNESS FOR A PARTICULAR PURPOSE AND 
NONINFRINGEMENT. IN NO EVENT SHALL THE AUTHORS OR COPYRIGHT HOLDERS BE LIABLE FOR ANY CLAIM, 
DAMAGES OR OTHER LIABILITY, WHETHER IN AN ACTION OF CONTRACT, TORT OR OTHERWISE, ARISING FROM, 
OUT OF OR IN CONNECTION WITH THE SOFTWARE OR THE USE OR OTHER DEALINGS IN THE SOFTWARE.
*/

/*
Clocks used in project:
After Power on reset:
Generic Clock Generator 0	- Enabled running from internal 8MHz
Generic Clock Generator 1	- Disabled
Generic Clock Generator 2	- Enabled running from internal 32Khz.
Generic Clock Generator 3-8 - Disabled

Arduino Setup will configure the clocks to:
Generic Clock Generator 0	- Enabled running 48MHz with GCG1 as reference to closed loop. (Used for USB, SERCOM, timers, GCM_EIC*, ADC, DAC)
Generic Clock Generator 1	- Enabled running from External 32KHz. (used for closed loop multiplier for GCG0) 
Generic Clock Generator 2	- Enabled running from internal 32KHz. (Used for Watchdog)
Generic Clock Generator 3	- Enabled running from internal 8MHz.
Generic Clock Generator 4   - Enabled running from internal 32KHz.  Used for Timer 3 (1 Hz interrupt).
Generic Clock Generator 5-8 - Disabled

*If set to sleep, and GCM_EIC clock is stopped, wakeup on external interrupt is not possible. GCM_EIC should be set to running clock (32khz) or so.

*/
#include <Arduino.h>
#include "main.h"
#include "Transponder_hal.h"
#include "timer.h"
#include "RFService.h"
#include "PCProtocol.h"
#include "FlashStorage.h"
#include "Adafruit_SleepyDog.h"

// for SPORT
#include "FrSkySportPollingDynamic.h"
#include "FrSkySportSensor.h"
#include "FrSkySportSensorGps.h"
#include "FrSkySportSensorPassthrough.h"
#include "FrSkySportSingleWireSerial.h"
#include "FrSkySportTelemetry.h"

// Mavlink Handling 
#include "MavlinkHandler.h"

void LowPowerTest(void);
void GoToSleep(void);
String base64_encode(byte[], int);
void BeaconService(void);
void One_second_Update(void);
void mavlinkSendADSB(float latitude, float longitude, uint8_t serverity, char *callsign);

FlashStorage(storedConfiguration, Configuration_t);

// Transponder Hardware abstraction layer
Transponder_hal systemHardware;

// System information
SystemInformation_t SystemInformation;

// FRSKY SPORT 
FrSkySportSensorGps FrskyGPS;             // Create GPS sensor with default ID
FrSkySportSensorGps FrskyGPS2(FrSkySportSensor::ID5);     // Create second GPS sensor (to be used in modulebay)
FrSkySportSensorPassthrough FrskyPASS;    // Create DIY sensor with default ID for Passthrough 
FrSkySportTelemetry FrskySport;           // Create telemetry object without polling
FrSkySportTelemetry FrskySportInModuleBay(new FrSkySportPollingDynamic(false));  // Create telemetry object with polling but disable the rxstatus (RSSI and Vbat tx part to radio)
MavlinkHandler MavlinkData;				  // Create Mavlink class to handle Mavlink from FC and pass it to Frsky Passthrough.

// Object for Radio communication
//RFService *RadioService = NULL;
RFService RadioService;

// Object for PC/User communication
PCProtocol serviceInterface;

/*
#define POWER_DOWN_DELAY  60 // Wait 60 seconds after power is lost before go to low power mode.
#define GPS_ON_TIME       60 //  60 seconds
#define GPS_OFF_TIME     600 // 600 seconds (10min)
*/
// DEBUG
//#define POWER_DOWN_DELAY  10 // Wait 60 seconds after power is lost before go to low power mode.
//#define GPS_ON_TIME       60 //  60 seconds
//#define GPS_OFF_TIME      10 // 600 seconds (10min)


void setup() {	
	// Init USB serial debug /setup:
	systemHardware.begin(); // Setup all pins according to hardware.
	Serial.begin(115200);

	uint32_t tempWDTCause = Watchdog.resetCause();
	/// Debug:
/*
	systemHardware.getSerialAUX()->println("");
	systemHardware.getSerialAUX()->print("Reset cause:" + String(tempWDTCause) + " ->");
	if(tempWDTCause == 1){
		systemHardware.getSerialAUX()->println("Power On Reset");
		}else if(tempWDTCause == 2){
		systemHardware.getSerialAUX()->println("1.2V Brownout!");
		}else if(tempWDTCause == 4){
		systemHardware.getSerialAUX()->println("3.3V Brownout!");
		}else if(tempWDTCause == 4){
		systemHardware.getSerialAUX()->println("3.3V Brownout!");
		}else if(tempWDTCause == 16){
		systemHardware.getSerialAUX()->println("External reset!");
		}else if(tempWDTCause == 32){
		systemHardware.getSerialAUX()->println("Watchdog!");
		/*
		do{
			systemHardware.LEDON();
			delay(50);
			systemHardware.LEDOFF();
			delay(50);
		}while(1);
		*//*
		}else if(tempWDTCause == 64){
		systemHardware.getSerialAUX()->println("System reset");
		}else{
		systemHardware.getSerialAUX()->println("Unknown");
	}
*/
	systemHardware.setBrownOut();
	
	SystemInformation.savedSettings = storedConfiguration.read();
	if(SystemInformation.savedSettings.valid == false){ // use default settings
		SystemInformation.savedSettings.isGroundstation = false;
		SystemInformation.savedSettings.POWER_DOWN_DELAY=60;   // Wait 60 seconds after power is lost before go to low power mode.
		SystemInformation.savedSettings.GPS_ON_TIME=60;		   //  60 seconds
		SystemInformation.savedSettings.GPS_OFF_TIME=600;	   // 600 seconds (10min)
		SystemInformation.savedSettings.BEACON_INTERVAL=10;   // every 10 seconds
		SystemInformation.savedSettings.callsign[0] = 'A'; 
		SystemInformation.savedSettings.callsign[1] = 'B'; 
		SystemInformation.savedSettings.callsign[2] = 'C'; 
		SystemInformation.savedSettings.callsign[3] = 'D'; 
		SystemInformation.savedSettings.callsign[4] = 'E'; 
		SystemInformation.savedSettings.callsign[5] = 'F'; 
		SystemInformation.savedSettings.callsign[6] = 'G'; 
		SystemInformation.savedSettings.callsign[7] = 'H';
		SystemInformation.savedSettings.callsign[8] = 0;
	}	
	String callsign = String("ADSB using callsign:" + String(SystemInformation.savedSettings.callsign));
	systemHardware.LEDSaftySwitchON();
	
	
	String resetCause = String("Watchdog reset cause:" + String(tempWDTCause));
	
	int firmwareMinor = round((SystemInformation.FIRMWARE_VERSION-(int)SystemInformation.FIRMWARE_VERSION)*100);	
	String firmwareVersion;
	if(firmwareMinor<10){
		firmwareVersion = String(String((int)SystemInformation.FIRMWARE_VERSION) + ".0" + String(firmwareMinor));
	}else{
		firmwareVersion = String(String((int)SystemInformation.FIRMWARE_VERSION) + "." + String(firmwareMinor));
	}	
	String startMSG = String("ADSB Initializing (ver. " + firmwareVersion + ") ");	

	// Init Auxiliary serial port:
	systemHardware.getSerialAUX()->begin(AUX_SERIAL_BAUDRATE);
	String auxSettings = String("ADSB Mavlink Baud@" + String(AUX_SERIAL_BAUDRATE));

	// Read the 128 bit serial number.
	//Serial.println("Chip unique serial number part 1:" + String(SystemInformation.SerialNumber1));
	//Serial.println("Chip unique serial number part 2:" + String(SystemInformation.SerialNumber2));
	//Serial.println("Chip unique serial number part 3:" + String(SystemInformation.SerialNumber3));
	//Serial.println("Chip unique serial number part 4:" + String(SystemInformation.SerialNumber4));
	//Serial.println("Chip unique serial number: \"" + String(SystemInformation.SerialNumber1) + String(SystemInformation.SerialNumber2) + String(SystemInformation.SerialNumber3) + String(SystemInformation.SerialNumber4)+"\"");
	#define SERIALNUMBER_SIZE 16
	uint8_t data[SERIALNUMBER_SIZE];
	data[0] = (byte)((SystemInformation.SerialNumber1 >> 24) & 0xFF);
	data[1] = (byte)((SystemInformation.SerialNumber1 >> 16) & 0xFF);
	data[2] = (byte)((SystemInformation.SerialNumber1 >> 8) & 0xFF);
	data[3] = (byte)(SystemInformation.SerialNumber1 & 0xFF);
	data[4] = (byte)((SystemInformation.SerialNumber2 >> 24) & 0xFF);
	data[5] = (byte)((SystemInformation.SerialNumber2 >> 16) & 0xFF);
	data[6] = (byte)((SystemInformation.SerialNumber2 >> 8) & 0xFF);
	data[7] = (byte)(SystemInformation.SerialNumber2 & 0xFF);
	data[8] = (byte)((SystemInformation.SerialNumber3 >> 24) & 0xFF);
	data[9] = (byte)((SystemInformation.SerialNumber3 >> 16) & 0xFF);
	data[10] = (byte)((SystemInformation.SerialNumber3 >> 8) & 0xFF);
	data[11] = (byte)(SystemInformation.SerialNumber3 & 0xFF);
	data[12] = (byte)((SystemInformation.SerialNumber4 >> 24) & 0xFF);
	data[13] = (byte)((SystemInformation.SerialNumber4 >> 16) & 0xFF);
	data[14] = (byte)((SystemInformation.SerialNumber4 >> 8) & 0xFF);
	data[15] = (byte)(SystemInformation.SerialNumber4 & 0xFF);
	
	// ADSB ID: "[BASE64CODE]"
	String base64MSG = String("ADSB ID:\"" + String(Telegram::base64_encode(data,SERIALNUMBER_SIZE).c_str()) + "\"");
	
	// Init the Radio protocol
//	RadioService = new RFService(systemHardware.getRadio(), &SystemInformation);
	RadioService.begin(systemHardware.getRadio(), &SystemInformation);
//	SerialProtocol = new PCProtocol(RadioService, Radio);

	String opperationMode;
	if(SystemInformation.savedSettings.isGroundstation){
		// Start the FrSky SPort library with polling using Serial port and only GPS2 second GPS:
		FrskySportInModuleBay.begin(systemHardware.getSerialFrSkySPort(), &FrskyGPS2);
		opperationMode = String("ADSB operating as groundstation");
	}else{
		// Start the FrSky SPort library with Serial port and the two sensors (GPS and Passthrought):
		FrskySport.begin(systemHardware.getSerialFrSkySPort(), &FrskyGPS, &FrskyPASS);		
		opperationMode = String("ADSB operating as transponder beacon");
	}
		
	// Start the Mavlink decoder and link it to FrSky GSP and Passthrough sensors for data update:
	MavlinkData.begin(systemHardware.getSerialAUX(), &FrskyGPS, &FrskyPASS);		

	// Set Timer 3 as 1 sec interrupt.
	startTimer3(1); // 1Hz
	//startTimer3(50); // 50Hz
	
	SystemInformation.state=STARTING_UP;
	systemHardware.PowerON(); // Ensure transponder keeps running from battery if external power is lost.
	systemHardware.PowerONGPSBackup(); // Enable backup power for GPS.
	SystemInformation.BatteryVoltage = systemHardware.getBatteryVoltage();
	SystemInformation.InputVoltage = systemHardware.getInputVoltage();
	SystemInformation.USBVoltage = systemHardware.getInputUSBVoltage();


	Serial.println(startMSG);
	Serial.println(resetCause);
	Serial.println(base64MSG);
	Serial.println(opperationMode);
	Serial.println(callsign);
	Serial.println(auxSettings);
	FrskyPASS.setDataTextMSG((char*)startMSG.c_str(), 7);  // ADSB Initializing (ver. 2.00)
	FrskyPASS.setDataTextMSG((char*)opperationMode.c_str(), 4);  // ADSB Mode (Groundstation or Beacon).	
	FrskyPASS.setDataTextMSG((char*)base64MSG.c_str(), 7); // ADSB ID: "[BASE64CODE]"
	FrskyPASS.setDataTextMSG((char*)callsign.c_str(), 7);  // ADSB using callsign [callsign]
	FrskyPASS.setDataTextMSG((char*)auxSettings.c_str(), 7); // ADSB Mavlink Baud@115200
	
	serviceInterface.begin(&SystemInformation);
	
//	systemHardware.getSerialAUX()->println("Debug start!");
//	delay(5000);
	Watchdog.enable(5000);
}

void loop() {

     //LowPowerTest();
/*
	 systemHardware.getSerialAUX()->println("Going to sleep!");
	 delay(100);
	 SystemInformation.SecondsSinceStart=20;
	 bool led = false;
	 systemHardware.PowerOFF();
	 do{
		Watchdog.reset();
		SCB->SCR |= SCB_SCR_SLEEPDEEP_Msk;
		SysTick->CTRL &= ~SysTick_CTRL_TICKINT_Msk;
		if(led){ systemHardware.LEDON(); led=false;}else{ systemHardware.LEDOFF();led=true;}
		__DSB();
		__WFI();
		SysTick->CTRL |= SysTick_CTRL_TICKINT_Msk;		 
	 }while(1);

	 
	 systemHardware.getSerialAUX()->println("Awake! -should not happen!");
	*/ 
	  
	do{
		One_second_Update();
		systemHardware.getGPS()->update();  // Function empty serial buffer and analyzes string.
		RadioService.Service();			    // Service the Radio module
		MavlinkData.service();				// Service the Mavlink data.
		BeaconService();				    // Time to make beacon for radio tx?
		if(serviceInterface.service()){
			Serial.println("Updating NVM parameters");
			SystemInformation.savedSettings.valid = true;
			storedConfiguration.write(SystemInformation.savedSettings);
		}
			
		
//		if(Serial.available()>0){
//			Serial.write(Serial.read());
//		}
			
		
		if(SystemInformation.SaftySwitchPushed == true){
			SystemInformation.state=POWER_OFF;
		}

		switch(SystemInformation.state)
		{
			case NORMAL: 
			{
				////// Below this line, code is executed fast!
				if(SystemInformation.SecondsBatteryLowCounter > 2){ // filter.
					SystemInformation.state=GET_READY_TO_RUN_ON_BATTERY;
				}else{
				    // normal fast loop.
//					SerialProtocol->Service(); // Comunincation to PC.
					if(SystemInformation.savedSettings.isGroundstation){
						FrskySportInModuleBay.send(); // FrskySport with pollling.					
					}else{
						FrskySport.send(); // Service the Serial for SPORT.
					}
				}			
			}
			break;
			 
			case GET_READY_TO_RUN_ON_BATTERY:
			{
				if(SystemInformation.SecondsBatteryLowCounter == 0){
					// Power is back!
					SystemInformation.state=NORMAL;
				}
				else{
					// check if it is time to go to battery 
					if(SystemInformation.SecondsBatteryLowCounter > SystemInformation.savedSettings.POWER_DOWN_DELAY){
						systemHardware.PowerONGPSBackup(); // Ensure backup power is enabled for GPS.
						SystemInformation.GPSActiveCounter=0; // ensure GPS active counter is reset.
						SystemInformation.state=RUNNING_ON_BATTERY_GPS_ON;
					}else{
//						SerialProtocol->Service(); // Comunincation to PC;
						FrskySport.send(); // Service the Serial for SPORT.
					}
				}
			} 
			break;
			
			case RUNNING_ON_BATTERY_GPS_ON:
			{
				if(SystemInformation.InputVoltage > 4.3 && (!SystemInformation.SimulateRunningOnBattery)){ // in debug mode force running on battery mode.
					SystemInformation.state=STARTING_UP;
				}else if(SystemInformation.BatteryVoltage <= 3.0){
					SystemInformation.state=POWER_OFF;
				}else{
					GoToSleep(); // Sleep until 1 sec interrupt will wake us up.
					if(++SystemInformation.GPSActiveCounter > SystemInformation.savedSettings.GPS_ON_TIME){ // power off GPS after 1 min.
						SystemInformation.GPSActiveCounter=0;
						delay(2000); // busy wait while GPS serial gets time to receive data from GPS (Unable in sleep mode).
						systemHardware.getGPS()->update();  // Service the GPS.
						systemHardware.PowerOFFGPS();// Turn OFF GPS main power.
						SystemInformation.state=RUNNING_ON_BATTERY_GPS_OFF;
					}
				}
			}
			break;

			case RUNNING_ON_BATTERY_GPS_OFF:
			{
				if( ((SystemInformation.InputVoltage > 4.3) || (SystemInformation.USBVoltage > 2.0 )) && (!SystemInformation.SimulateRunningOnBattery)){ // in debug mode force running on battery mode.
					SystemInformation.state=STARTING_UP;
					}else if(SystemInformation.BatteryVoltage <= 3.0){
						SystemInformation.state=POWER_OFF;
					}else{
						GoToSleep(); // Sleep until 1 sec interrupt will wake us up.
						if(++SystemInformation.GPSActiveCounter > SystemInformation.savedSettings.GPS_OFF_TIME){ // Turn on GPS if off time is meet.
							SystemInformation.GPSActiveCounter=0;
							systemHardware.PowerONGPS();// Turn OFF GPS main power.
							SystemInformation.state=RUNNING_ON_BATTERY_GPS_ON;
						}
				}
			}
			break;


			case POWER_OFF:
			{
				systemHardware.PowerOFF(); 
				Serial.println("ADSB Status: Power OFF - Please remove power.");		
				do{
					// CPU should have died here, but if we are still powered the flash fast led.
					systemHardware.LEDON();
					systemHardware.LEDSaftySwitchON();
					delay(50);
					systemHardware.LEDOFF();
					systemHardware.LEDSaftySwitchOFF();
					delay(50);
				}while(1);
			}
			break;			


			case STARTING_UP:
			{
				systemHardware.PowerONGPS();// Turn on GPS.
				// Set the radio to RX mode without timeout.
				SystemInformation.SecondCounter=0; // reset second counter.
				SystemInformation.SecondsBatteryLowCounter = 0;
				SystemInformation.state=NORMAL;		
			}
			break;
			 
			default:
				SystemInformation.state = STARTING_UP;
			break;
		}
	}while(1); 
}

void GoToSleep(void){
	RadioService.PowerDown();
	systemHardware.auxSerialPowerDown();
	systemHardware.PowerOFFFrSkySmartPort();

	if(SystemInformation.SecondsSinceStart > 10){ // Don't sleep the first 10 seconds after power on.
		USBDevice.detach();
		SCB->SCR |= SCB_SCR_SLEEPDEEP_Msk;
		
		SysTick->CTRL &= ~SysTick_CTRL_TICKINT_Msk;
		__DSB();
		__WFI();
		SysTick->CTRL |= SysTick_CTRL_TICKINT_Msk;
	
		// Wake up:
		USBDevice.attach();
	}

	systemHardware.PowerONFrSkySmartPort();
	systemHardware.auxSerialPowerUp();
	RadioService.WakeUp();	
}

void LowPowerTest(void){
	systemHardware.PowerOFFGPS(); // Turn off  GPS to save battery.
	systemHardware.PowerOFFGPSBackup(); // Ensure backup power is enabled for GPS.	
	systemHardware.LEDSaftySwitchOFF();
	systemHardware.PowerOFFFrSkySmartPort();
	systemHardware.LEDOFF();
	do
	{
		GoToSleep();
	}while(1);
}

// Ensure a beacon is transmitted every N second.
void BeaconService(void){
	if(SystemInformation.BeaconSecondCounter >= SystemInformation.savedSettings.BEACON_INTERVAL){ // SystemInformation.BeaconSecondCounter is counted up en Timer3 (1Hz) ISR.
//		SerialAUX->print("Time to make beacon message...");
		// Send a Standard beacon:
		SystemInformation.BeaconSecondCounter =  0; // Reset Beacon counter.
		if(SystemInformation.savedSettings.isGroundstation==false){
			// Serial print status:
			Serial.print("Transponder Status: Battery=" + String(SystemInformation.BatteryVoltage,2) + "V ");
			if(systemHardware.GetChargeState() == HIGH){
				Serial.print("(Complete)");
				}else{
				Serial.print("(Charging)");
			}
			Serial.println(" SaftySwitch:" + String(systemHardware.SaftySwitchPushed()) + "|" + String(SystemInformation.SafteSwitchPushedTimer) + "|" + String(SystemInformation.SaftySwitchFirstTimePushed));
			
			// update system with latest GPS values;
//			Serial.println("Sending Beacon: " + String(systemHardware.getGPS()->getLatitude()) + "," + String(systemHardware.getGPS()->getLongitude()));
			SystemInformation.UTCTime = systemHardware.getGPS()->getUTCTime();
			SystemInformation.Latitude = systemHardware.getGPS()->getLatitude();
			SystemInformation.Longitude = systemHardware.getGPS()->getLongitude();
			SystemInformation.NumberOfSat = systemHardware.getGPS()->getNumberOfSat();
			SystemInformation.Fix = systemHardware.getGPS()->getFix();
			SystemInformation.hdop = systemHardware.getGPS()->getHDOP();
			RadioService.SendBeacon();
		}else{
//			SerialAUX->println("Im groundstation, NoPing!");
		}
//		SerialAUX->println("Done!");	
	}else{ // see if there are any messages from radio to Mavlink / FrSky.
		
		transponderData_t *temp = RadioService.getRadioText();		
		if(temp->dataReady){
			FrskyPASS.setDataTextMSG(temp->data, temp->servirity);

			// Make Mavlink ADSB msg:
	//		systemHardware.getSerialAUX()->println("Data ready for Mavlink:");
			mavlinkSendADSB(temp->latitude,temp->longitude,temp->servirity, SystemInformation.savedSettings.callsign);
			FrskyGPS2.setData(temp->latitude,temp->longitude,0,0,0,0,0,0,0,0,0); // Set second GPS data on SPORT (for module bay) when groundstation.
			temp->dataReady=false;
		}
	}	
}

void One_second_Update(void){
	//// only every second (check status)
	while(SystemInformation.SecondCounter){
		Watchdog.reset();
		SystemInformation.SecondCounter--;
		SystemInformation.BatteryVoltage = systemHardware.getBatteryVoltage();
		SystemInformation.InputVoltage = systemHardware.getInputVoltage();
		SystemInformation.USBVoltage = systemHardware.getInputUSBVoltage();				
		
		if( ((SystemInformation.InputVoltage <= 4.3) && (SystemInformation.USBVoltage <=2 )) || (SystemInformation.SimulateRunningOnBattery)){
			if(SystemInformation.SecondsBatteryLowCounter < 255){
				SystemInformation.SecondsBatteryLowCounter++;
			}
		}else{
			SystemInformation.SecondsBatteryLowCounter=0;
		}			
	
		if(systemHardware.SaftySwitchPushed())
		{			
			SystemInformation.SafteSwitchPushedTimer++;
			if(SystemInformation.SafteSwitchPushedTimer == 2){
				systemHardware.LEDSaftySwitchON();
				SystemInformation.SaftySwitchFirstTimePushed=true;
			}else if(SystemInformation.SafteSwitchPushedTimer >= 4){
				systemHardware.LEDSaftySwitchOFF();
				SystemInformation.SaftySwitchFirstTimePushed=false;
			}
		}else{
			if(SystemInformation.SaftySwitchFirstTimePushed==true)
			{
				for(int a=0;a<10;a++)
				{
					systemHardware.LEDSaftySwitchOFF();
					delay(50);
					systemHardware.LEDSaftySwitchON();
					delay(50);
				}
				SystemInformation.SaftySwitchFirstTimePushed=false;
				SystemInformation.SaftySwitchPushed=true;
			}else
			{
				SystemInformation.SafteSwitchPushedTimer=0;
			}
		}
		
		if(SystemInformation.SecondsSinceStart > 5 && !SystemInformation.SaftySwitchFirstTimePushed){
			systemHardware.LEDSaftySwitchOFF();
		}
		
		if(systemHardware.getGPS()->dataIsValid()){
			if(SystemInformation.gpsValidSentOnlyOnce == false){
				String text = String("ADSB local GPS sensor detected");
				FrskyPASS.setDataTextMSG((char*)text.c_str(), 7);		
				Serial.println(text);		
				SystemInformation.gpsValidSentOnlyOnce=true;
			}
		}
		/*
		Serial.print("Transponder Status: Battery=" + String(SystemInformation.BatteryVoltage,2) + "V ");
		if(systemHardware.GetChargeState() == HIGH){
			Serial.print("(Complete)");		
		}else{
			Serial.print("(Charging)");					
		}
		Serial.println(" SaftySwitch:" + String(systemHardware.SaftySwitchPushed()) + "|" + String(SystemInformation.SafteSwitchPushedTimer) + "|" + String(SystemInformation.SaftySwitchFirstTimePushed));
		*/
	}
}
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

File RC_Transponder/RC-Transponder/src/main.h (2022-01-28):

/*
	main.h

	Copyright (c) 2019 Lagoni
	Not for commercial use
 */ 


#ifndef MAIN_H_
#define MAIN_H_

#include "Transponder_hal.h"

enum TRANSPONDER_STATES {
	STARTING_UP,
	NORMAL,
	GET_READY_TO_RUN_ON_BATTERY,
	RUNNING_ON_BATTERY_GPS_ON,
	RUNNING_ON_BATTERY_GPS_OFF,
	POWER_OFF
};

typedef struct {
	boolean valid;
	boolean isGroundstation;
	uint32_t POWER_DOWN_DELAY;
	uint32_t GPS_ON_TIME;
	uint32_t GPS_OFF_TIME;
	uint8_t BEACON_INTERVAL;
	char callsign[9];
}Configuration_t;

extern struct SystemInformation_t
{	
	// Hardware and Software version defines
	const float FIRMWARE_VERSION = 2.09;
	//const uint8_t pcbVersion = PCB_VERSION;
	const uint8_t pcbVersion = PCB_VERSION;
	
	// Counters
	uint8_t SecondCounter = 0;
	uint8_t BeaconSecondCounter = 0;
	uint32_t SecondsSinceStart = 0;

	// system overall statemachine
	enum TRANSPONDER_STATES state=STARTING_UP;

	float BatteryVoltage = 0;
	float InputVoltage = 0;
	float USBVoltage = 0;

	//Serial number:
	volatile uint32_t *AddrSerialNumber1 = (volatile uint32_t *)0x0080A00C;
	uint32_t SerialNumber1= *AddrSerialNumber1;
	volatile uint32_t *AddrSerialNumber2 = (volatile uint32_t *)0x0080A040;
	uint32_t SerialNumber2= *AddrSerialNumber2;
	volatile uint32_t *AddrSerialNumber3 = (volatile uint32_t *)0x0080A044;
	uint32_t SerialNumber3= *AddrSerialNumber3;
	volatile uint32_t *AddrSerialNumber4 = (volatile uint32_t *)0x0080A048;
	uint32_t SerialNumber4= *AddrSerialNumber4;	

	uint8_t SecondsBatteryLowCounter = 0;
	bool SimulateRunningOnBattery = false;
	uint16_t GPSActiveCounter = 0;
	uint8_t SafteSwitchPushedTimer=0;
	bool SaftySwitchFirstTimePushed =0;
	bool SaftySwitchPushed =0;
	
	// Local GPS Data:
	uint32_t UTCTime=0;
	int32_t Latitude=0;   // 1E7
	int32_t Longitude=0;
	uint8_t  NumberOfSat=0;
	uint8_t  Fix=0;
	float hdop=0;
	float groundspeed=0; // not used yet (not extracted from GPS)
	
	bool gpsValidSentOnlyOnce=false;
	
	Configuration_t savedSettings;
}SystemInformation;



#endif /* MAIN_H_ */

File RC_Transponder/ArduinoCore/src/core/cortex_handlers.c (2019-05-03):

/*
  Copyright (c) 2015 Arduino LLC.  All right reserved.

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
  You should have received a copy of the GNU Lesser General Public
  License along with this library; if not, write to the Free Software
  Foundation, Inc., 51 Franklin St, Fifth Floor, Boston, MA  02110-1301  USA
*/

#include <sam.h>
#include <variant.h>
#include <stdio.h>

/* RTOS Hooks */
extern void svcHook(void);
extern void pendSVHook(void);
extern int sysTickHook(void);

uint32_t phantomISR = 9999;

/* Default empty handler */
void Dummy_Handler(void)
{
	uint32_t a,b = 0;

	#if defined DEBUG
	__BKPT(3);
	#endif

	for (;;) 
	{
		for(b=0;b<10;b++)
		{
		
		  for(a=0;a<25000;a++) 
		  {
		   digitalWrite(21, 0); 
		   asm volatile ("nop"::);
		  }

		  for(a=0;a<25000;a++) 
		  {	
			digitalWrite(21, 1); 
		    asm volatile ("nop"::);
		  }
		}
		for(a=0;a<2500000;a++)  {asm volatile ("nop"::); }  
	}
}


/* Cortex-M0+ core handlers */
void HardFault_Handler(void) __attribute__ ((weak, alias("Dummy_Handler")));
void Reset_Handler    (void);
void NMI_Handler      (void) __attribute__ ((weak, alias("Dummy_Handler")));
void SVC_Handler      (void) __attribute__ ((weak, alias("Dummy_Handler")));
void PendSV_Handler   (void) __attribute__ ((weak, alias("Dummy_Handler")));
void SysTick_Handler  (void);

/* Peripherals handlers */
void PM_Handler       (void) __attribute__ ((weak, alias("Dummy_Handler")));
void SYSCTRL_Handler  (void) __attribute__ ((weak, alias("Dummy_Handler")));
void WDT_Handler      (void) __attribute__ ((weak, alias("Dummy_Handler")));
void RTC_Handler      (void) __attribute__ ((weak, alias("Dummy_Handler")));
void EIC_Handler      (void) __attribute__ ((weak, alias("Dummy_Handler")));
void NVMCTRL_Handler  (void) __attribute__ ((weak, alias("Dummy_Handler")));
void DMAC_Handler     (void) __attribute__ ((weak, alias("Dummy_Handler")));
void USB_Handler      (void) __attribute__ ((weak));
void EVSYS_Handler    (void) __attribute__ ((weak, alias("Dummy_Handler")));
void SERCOM0_Handler  (void) __attribute__ ((weak, alias("Dummy_Handler")));
void SERCOM1_Handler  (void) __attribute__ ((weak, alias("Dummy_Handler")));
void SERCOM2_Handler  (void) __attribute__ ((weak, alias("Dummy_Handler")));
void SERCOM3_Handler  (void) __attribute__ ((weak, alias("Dummy_Handler")));
void SERCOM4_Handler  (void) __attribute__ ((weak, alias("Dummy_Handler")));
void SERCOM5_Handler  (void) __attribute__ ((weak, alias("Dummy_Handler")));
void TCC0_Handler     (void) __attribute__ ((weak, alias("Dummy_Handler")));
void TCC1_Handler     (void) __attribute__ ((weak, alias("Dummy_Handler")));
void TCC2_Handler     (void) __attribute__ ((weak, alias("Dummy_Handler")));
void TC3_Handler      (void) __attribute__ ((weak, alias("Dummy_Handler")));
void TC4_Handler      (void) __attribute__ ((weak, alias("Dummy_Handler")));
void TC5_Handler      (void) __attribute__ ((weak)); // Used in Tone.cpp
void TC6_Handler      (void) __attribute__ ((weak, alias("Dummy_Handler")));
void TC7_Handler      (void) __attribute__ ((weak, alias("Dummy_Handler")));
void ADC_Handler      (void) __attribute__ ((weak, alias("Dummy_Handler")));
void AC_Handler       (void) __attribute__ ((weak, alias("Dummy_Handler")));
void DAC_Handler      (void) __attribute__ ((weak, alias("Dummy_Handler")));
void PTC_Handler      (void) __attribute__ ((weak, alias("Dummy_Handler")));
void I2S_Handler      (void) __attribute__ ((weak, alias("Dummy_Handler")));

/* Initialize segments */
extern uint32_t __etext;
extern uint32_t __data_start__;
extern uint32_t __data_end__;
extern uint32_t __bss_start__;
extern uint32_t __bss_end__;
extern uint32_t __StackTop;

/* Exception Table */
__attribute__ ((section(".isr_vector"))) const DeviceVectors exception_table =
{
  /* Configure Initial Stack Pointer, using linker-generated symbols */
  (void*) (&__StackTop),

  (void*) Reset_Handler,
  (void*) NMI_Handler,
  (void*) HardFault_Handler,
  (void*) (0UL), /* Reserved */
  (void*) (0UL), /* Reserved */
  (void*) (0UL), /* Reserved */
  (void*) (0UL), /* Reserved */
  (void*) (0UL), /* Reserved */
  (void*) (0UL), /* Reserved */
  (void*) (0UL), /* Reserved */
  (void*) SVC_Handler,
  (void*) (0UL), /* Reserved */
  (void*) (0UL), /* Reserved */
  (void*) PendSV_Handler,
  (void*) SysTick_Handler,

  /* Configurable interrupts */
  (void*) PM_Handler,             /*  0 Power Manager */
  (void*) SYSCTRL_Handler,        /*  1 System Control */
  (void*) WDT_Handler,            /*  2 Watchdog Timer */
  (void*) RTC_Handler,            /*  3 Real-Time Counter */
  (void*) EIC_Handler,            /*  4 External Interrupt Controller */
  (void*) NVMCTRL_Handler,        /*  5 Non-Volatile Memory Controller */
  (void*) DMAC_Handler,           /*  6 Direct Memory Access Controller */
  (void*) USB_Handler,            /*  7 Universal Serial Bus */
  (void*) EVSYS_Handler,          /*  8 Event System Interface */
  (void*) SERCOM0_Handler,        /*  9 Serial Communication Interface 0 */
  (void*) SERCOM1_Handler,        /* 10 Serial Communication Interface 1 */
  (void*) SERCOM2_Handler,        /* 11 Serial Communication Interface 2 */
  (void*) SERCOM3_Handler,        /* 12 Serial Communication Interface 3 */
  (void*) SERCOM4_Handler,        /* 13 Serial Communication Interface 4 */
  (void*) SERCOM5_Handler,        /* 14 Serial Communication Interface 5 */
  (void*) TCC0_Handler,           /* 15 Timer Counter Control 0 */
  (void*) TCC1_Handler,           /* 16 Timer Counter Control 1 */
  (void*) TCC2_Handler,           /* 17 Timer Counter Control 2 */
  (void*) TC3_Handler,            /* 18 Basic Timer Counter 0 */
  (void*) TC4_Handler,            /* 19 Basic Timer Counter 1 */
  (void*) TC5_Handler,            /* 20 Basic Timer Counter 2 */
  (void*) TC6_Handler,            /* 21 Basic Timer Counter 3 */
  (void*) TC7_Handler,            /* 22 Basic Timer Counter 4 */
  (void*) ADC_Handler,            /* 23 Analog Digital Converter */
  (void*) AC_Handler,             /* 24 Analog Comparators */
  (void*) DAC_Handler,            /* 25 Digital Analog Converter */
  (void*) PTC_Handler,            /* 26 Peripheral Touch Controller */
  (void*) I2S_Handler,            /* 27 Inter-IC Sound Interface */
  (void*) (0UL),                  /* Reserved */
};

extern int main(void);

/* This is called on processor reset to initialize the device and call main() */
void Reset_Handler(void)
{
  uint32_t *pSrc, *pDest;

  /* Initialize the initialized data section */
  pSrc = &__etext;
  pDest = &__data_start__;

  if ((&__data_start__ != &__data_end__) && (pSrc != pDest)) {
    for (; pDest < &__data_end__; pDest++, pSrc++)
      *pDest = *pSrc;
  }

  /* Clear the zero section */
  if ((&__data_start__ != &__data_end__) && (pSrc != pDest)) {
    for (pDest = &__bss_start__; pDest < &__bss_end__; pDest++)
      *pDest = 0;
  }

  SystemInit();

  main();

  while (1)
    ;
}

/* Default Arduino systick handler */
extern void SysTick_DefaultHandler(void);
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

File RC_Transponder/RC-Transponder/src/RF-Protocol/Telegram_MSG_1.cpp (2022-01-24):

/*
	Telegram_MSG_1.cpp

	Copyright (c) 2019 Lagoni
	Not for commercial use
 */ 
  #include "Telegram_MSG_1.h"
  
// constructor 
Telegram_MSG_1::Telegram_MSG_1(uint32_t _Unique_ID_1, uint32_t _Unique_ID_2, uint32_t _Unique_ID_3, uint32_t _Unique_ID_4, 
							   uint32_t _UTCTime,  int32_t _Lattitude, int32_t _Longitude, uint8_t _NumberOfSat, uint8_t _Fix,
							   bool _RunningOnBattery, float _HDOP, float _GroundSpeed, uint8_t _SecondsSinceLastGSContact,
							   float _BatteryVoltage, float _FirmwareVersion, uint8_t _PCBVersion, uint8_t _NumberOfBeaconsToRelay, char *_callsign)
							   : Telegram(MSG_Beacon_Broadcast, _Unique_ID_1, _Unique_ID_2, _Unique_ID_3, _Unique_ID_4)
{	
	this->setData(_Unique_ID_1, _Unique_ID_2, _Unique_ID_3, _Unique_ID_4,
	_UTCTime,  _Lattitude, _Longitude, _NumberOfSat, _Fix,
	_RunningOnBattery, _HDOP, _GroundSpeed, _SecondsSinceLastGSContact,
	_BatteryVoltage, _FirmwareVersion, _PCBVersion, _NumberOfBeaconsToRelay, _callsign);

/*
	//Payload
	this->UTCTime = _UTCTime;
	this->Latitude = _Lattitude;
	this->Longitude = _Longitude;			
	this->NumberOfSat = _NumberOfSat;
	this->Fix = _Fix;
	this->RunningOnBattery = _RunningOnBattery;
	this->HDOP = _HDOP;
	this->GroundSpeed = _GroundSpeed;
	this->SecondsSinceLastGSContact = _SecondsSinceLastGSContact;
	this->BatteryVoltage = _BatteryVoltage;
	this->FirmwareVersion = _FirmwareVersion;
	this->PCBVersion = _PCBVersion;
	this->NumberOfBeaconsToRelay = _NumberOfBeaconsToRelay;
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

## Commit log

2019-02-11 First Commit
    First Commit
    [arduino_zero.cfg]
2019-02-11 First Commit
    Hardware -10 and -11
    [RC-TranponderV11.brd, RCTransponder-10.brd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]
2019-03-30 PCprotocol fixed and reveive memory leak fixed
    [PCProtocol.cpp, RFProtocol.cpp, main.cpp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]
2019-04-04 Issue with RF statemachine
    [PCProtocol.cpp, RFProtocol.cpp, Telegram_MSG_1.cpp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]
2019-04-04 Bootloader with UART dissable and LED changed to LED on transponder.
2019-04-05 Still some relay problems
    [GPSL80Lite.cpp, RFProtocol.cpp, Telegram_MSG_1.cpp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]
2019-04-05 SavedBeacons changed to arrays og object (stack) instead of arrays of pointers to objects (HEAP). This seams to fix the issue where the USB deltes te points. Also Push button function added
    [RFProtocol.cpp, Telegram_MSG_1.cpp, Telegram_MSG_2.cpp]
2019-04-30 Making RF protocol platform indenpenden
    Splitting RF part into Service and Protocol to make Protocol part platform independen and easyer to port to Raspberry Pi
2019-05-01 Telegram and RFprotocol ready for cross platform
    Ensure Telegram and RFprotocol is not hardware dependen (Arduino)
    Make Base64 encode/decode static
2019-05-01 Added Groundstation code
    Code added
2019-05-02 printf
    printf
2022-01-05 SerialAUX removed as debug print
    We want to start using SerialAUX as Mavlink / ADSB communication.
2022-01-05 Added Serial Print out as "NMEA" to USB serial port.
    The PC protocol has been removed and for now when a MSG1 (Beacon) is received, it is simply printet out as text to USB serial.
2022-01-11 Added PassThrough sensor to SPORT Lib.
2022-01-14 Telegram MSG1 updated
    Pressure parameter(never implemented) changed to HDOP.
    [PowerConsumption.xlsx]
2022-01-14 Passthrough loop optimized.
    Now each High and Low loop can give time slot to each other if not data is ready.
2022-01-14 Adding power cycle to GPS on boot
2022-01-14 Variant.cpp changed to use PIO_SERCOM_ALT as defautl for PIN 8,9 (GPS RX/TX)
2022-01-14 Groundstation removed from ADSB Transponder branch, it is not used here.
2022-01-18 Changing structure so all classes are initlized at start, to avoid the use of new and delete.
    [GPSL80Lite.cpp, PCProtocol.cpp, RFProtocol.cpp]
2022-01-24 Added Watchdog and brownout.
    [Transponder_hal.cpp, Transponder_hal.h]
2022-01-24 Removed debug printout
2022-01-24 Timer 3 moved to Generic Clock Generator 4, because Watchdog lib (sleepy dog) uses GCG2.
2022-01-24 Adding Firmware Release v2.00 for PCBA Version -11 and -12
2022-01-25 Release of Hardware version 12
    [BOM.csv, RC-TranponderV12.brd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]
2022-01-27 Added printout of GPS power timing
2022-01-28 Added support for Groundstation mode "setmode 1/0"
